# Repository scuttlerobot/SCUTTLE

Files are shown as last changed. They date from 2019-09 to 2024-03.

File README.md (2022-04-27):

# SCUTTLE™ Robot
This repository contains software (embedded Linux & Python) and hardware design files for the SCUTTLE Project.

### Sensing, Connected, Utility Transport Taxi for Level Environments
* payload capable (40kg)
* maker-friendly
* open source
* low-cost

### Visit the [SCUTTLE™ Webpage](https://scuttlerobot.org).
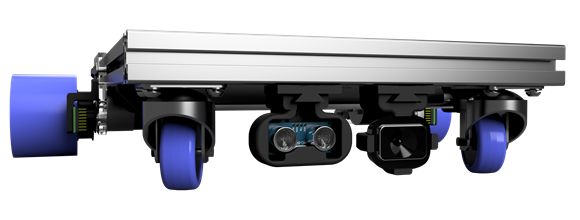
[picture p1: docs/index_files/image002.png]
SCUTTLE Robot


### License
This work is licensed under the Creative Commons Attribution-ShareAlike 4.0 License.  To view details [visit creativecommons.org](https://creativecommons.org/licenses/by-sa/4.0/legalcode)

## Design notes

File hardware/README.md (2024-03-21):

# SCUTTLE™ Hardware
This directory contains hardware for standard SCUTTLE components.
* STL files for 3D printing
* 2D Drawings

Note: heavy models and elaborate CAD is stored OUTSIDE github to keep the repository lightweight.

## Jump to V3.0 model
Full assembly is posted on grabCAD
[grabCAD SCUTTLE v3.0](https://grabcad.com/library/scuttle-robot-v3-0-1)
As upgrades are made to individual systems, we post individual models and describe them at scuttlerobot.org.

## Important models
Are archived on our website at
[scuttlerobot.org/resources/models](https://https://www.scuttlerobot.org/resources/models/)

## Native CAD files
Are primarily posted on grabCAD using keyword: "scuttle robot"
[search grabCAD](https://grabcad.com/library?page=2&time=all_time&sort=recent&query=scuttle%20robot)

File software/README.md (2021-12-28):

# SCUTTLE Software
This folder contains all scuttle software and software information.

<br>

## SHELL Processes Cheat Sheet:
**Remove your Tamulink WPA credentials from the device:**
* Navigate to the connmanctl folder located at /var/lib/connman$
* Find the configuration file with extension .config
* remove the config file with "rm."  Example: 
```
debian@scuttle:/var/lib/connman$ sudo rm wifi_8030dc035d88_74616d756c696e6b2d777061_managed_ieee8021x.config
  ```

**Report devices active on the i2c bus:**
```
sudo i2cdetect -y -r 1

  sudo:       Executes the command following as root user
  i2cdetect:  A program to scan an I2C bus for devices
  -y  :       Does not prompt
  -r 1:       I2C bus to read from. Here we read from I2C bus 1.
  ```

**Report the messages from kernel ring buffer (system architecture, cpu, attached devices, etc)**
```
dmesg
  ```
  
**Check battery voltage (with example output)**
```
➜  ~ sudo rc_battery_monitor
2S Pack   Jack   #Cells   Cell
 8.22V   10.63V  3       3.54V   [1]    1088 killed     sudo rc_battery_monitor

  ```
**List USB devices connected (with example output)**
  ```
➜  ~ lsusb
Bus 001 Device 003: ID 2f24:0091
Bus 001 Device 001: ID 1d6b:0002 Linux Foundation 2.0 root hub
  ```

**Explicitly Show Debian Release Date**
  ```
debian@scuttle:~$ cat /etc/dogtag
BeagleBoard.org Debian Image 2018-10-07

  ```
  
**Check if you have a live internet connection**
  ```
debian@scuttle:~$ ping google.com
PING google.com (216.58.194.110) 56(84) bytes of data.
64 bytes from dfw06s48-in-f14.1e100.net (216.58.194.110): icmp_seq=1 ttl=55 time                                       =10.5 ms
64 bytes from dfw06s48-in-f14.1e100.net (216.58.194.110): icmp_seq=2 ttl=55 time                                       =16.3 ms
64 bytes from dfw06s48-in-f14.1e100.net (216.58.194.110): icmp_seq=3 ttl=55 time                                       =17.8 ms
64 bytes from dfw06s48-in-f14.1e100.net (216.58.194.110): icmp_seq=4 ttl=55 time                                       =16.5 ms
^C
--- google.com ping statistics ---
4 packets transmitted, 4 received, 0% packet loss, time 3005ms
rtt min/avg/max/mdev = 10.521/15.320/17.869/2.835 ms
  ```

**Manually Connect to the internet**
<br>
Use commands: sudo connmanctl, scan wifi, agent on, services, connect (service)
<br>
[see steps and example output here](https://gist.github.com/dmalawey/e4be9f3b5beba8ed49868065935127b7)

**Copy a GitHub repository to your device**
  ```
debian@scuttle:~$ git clone http://github.com/scuttlerobot/SCUTTLE
Cloning into 'SCUTTLE'...
remote: Enumerating objects: 262, done.
remote: Counting objects: 100% (262/262), done.
remote: Compressing objects: 100% (215/215), done.
remote: Total 1356 (delta 128), reused 99 (delta 41), pack-reused 1094
Receiving objects: 100% (1356/1356), 82.88 MiB | 1.17 MiB/s, done.
Resolving deltas: 100% (610/610), done.
debian@scuttle:~$
  ```

**Expand the partition on your Blue SD card**
  ```
cd /opt/scripts/tools #navigate to the right directory
git pull  #update the tools repository
sudo ./grow_partition.sh  # the command to expand the boot partition
sudo reboot # the command to reboot the blue
  ```
  
**Print the current connections**
  ```
sudo iwconfig
  ```
  
**Copy a github repository**
  ```
git clone http://www.github.com/scuttlerobot/SCUTTLE
  ```
  This will copy all of the contents of SCUTTLE repo into a folder called SCUTTLE in the working directory.
  
**github - push updates from local to online repository**
  ```
git add -A
git commit -m # then make brief comment on your update
git push # then provide credentials as needed
  ```
  This will push the updates from your local device back to the online repo.

**github - pull updates from online to local repository**
  ```
git pull
  ```
  This will pull updates from online.  If it has conflicts and you want to force it, follow the steps in [this link](https://learn.adafruit.com/an-introduction-to-collaborating-with-version-control/https-credential-caching-and-ssh-keys).
  
## Windows Cheat Sheet:
**find out the IP address of a connected device**
Press the windows key, type "cmd" then ENTER.  In the command prompt, type ipconfig.  If you are connected to your linux device that is in access-point mode with your wireless wifi adapter, look at Wireless LAN section and the Default Gateway is the IP address of your linux device.

```
Wireless LAN adapter Wi-Fi:
   Connection-specific DNS Suffix  . :
   Link-local IPv6 Address . . . . . : fe80::8123:73e7:ace0:720c%15
   IPv4 Address. . . . . . . . . . . : 192.168.50.50
   Subnet Mask . . . . . . . . . . . : 255.255.255.0
   Default Gateway . . . . . . . . . : 192.168.50.1
```

## Beaglebone Blue Cheat Sheet:

**Default Wifi**
<br>Access Point SSID: BeagleBone-XXXX
<br>Password: BeagleBone

**Need extra help troubleshooting?**
<br/>
([beaglebone Live Chat](https://beagleboard.org/chat))
<br/>
Make sure 1) it's a beagle related issue 2) you give 30 minutes for an expert to respond (they will!) before you close the window. 3) If you learn something helpful for the project, share with our github admins

**Important ip addresses:**
<br/>
192.168.8.1:22 default terminal session over wifi <br/>
192.168.7.2:22 default terminal session over USB <br/>
192.168.8.1:3000 Cloud9 (over wifi) <br/>
192.168.8.1:1880 Nodered (over wifi) <br/>

**Instructions to connect to SSH using putty:**
<br/>
([beaglebone how-to-connect](https://www.dummies.com/computers/beaglebone/how-to-connect-your-beaglebone-via-ssh-over-usb/))

**Instructions to flash a new SD card with an image:**
<br/>
([beagleboard.org getting started](http://beagleboard.org/getting-started#step3))

**Access NodeRed:**
<br/>
Navigate to nodered: 192.168.8.1:1880

**Reinstall RCPY/librobotcontrol if it becomes corrupted**
<br/>
sudo apt-get purge roboticscape <br/>
sudo apt-get install librobotcontrol

**A Tool for Pin Checking:**
<br/>
This tool is great for debugging connections to pins. <br/>
([Pin configuration viewer tool, nicely formatted.](https://github.com/mvduin/bbb-pin-utils/tree/blue#show-pins))

## Raspberry Pi Cheat Sheet:
**Instructions to connect to SSH using putty:**
([beaglebone how-to-connect](https://www.dummies.com/computers/beaglebone/how-to-connect-your-beaglebone-via-ssh-over-usb/))

**Instructions to flash a new SD card with an image:**
([beagleboard.org getting started](http://beagleboard.org/getting-started#step3))

**broadcom BCM pin numbering scheme:**
https://gpiozero.readthedocs.io/en/stable/recipes.html#pin-numbering

# Linux Cheatsheet

### File System Navigation and Information

`ls` - **List** - List the files and folders in a directory.<br>
`cd` - **Change Directory** - Move into a folder.<br>
`pwd` - **Print Working Directory** - Prints your current location to the terminal.<br>
`cp` - **Copy** - Copies a file from a location, to a location.<br>
`mv` - **Move** - Moves a file from a location, to a location.<br>
`touch` - **Touch** - Create a file.<br>
`mkdir` - **Make Directory** - Make a directory with given name.<br>
`nano` - File editor.<br>
`cat` - **Concatenate** - Concatenate files and print file contents to the terminal.<br>
`head` - Output the first part of files.<br>
`tail` - Output the last part of files.<br>
`more` - View a file and scroll through it.<br>
`less` - View a file and scroll through it. (Consumes less resources than `more`)<br>
`rm` - **Remove** - Remove files or directories.<br>
`rmdir` - **Remove Directory** - Remove empty directories.<br>
`file` - Determine file type.<br>

### System and User Info

`whoami` - **Who Am I?** - Print current user.<br>
`date` - Print or set the system date and time.<br>
`df` - Report file system disk space usage.<br>
`which` - Locate a command.<br>
`whereis` - Locate the binary, source, and manual page files for a command.<br>

### Searching

`grep` - Print lines that match patterns.<br>
`locate` - Find files by name.<br>

### Administrator

`sudo` - **Superuser Do** - Execute a command as root(superuser).<br>
`sudo su` - Switch to the root user.<br>

### Modify Permissions

`chown` - **Change Owner** - Change ownership of a file.<br>
`chmod` - **Change Mode** - Change file mode bits.<br>

### Network Information

`ping` - Send ICMP ECHO_REQUEST to network hosts.<br>
`ifconfig` - Configure a network interface.<br>
`iwconfig` - Configure a wireless network interface.<br>
`connmanctl` - **Connection Manager** - WiFi connection Utility.<br>

### Web Tools

`wget` - **Web Get** - Get a file from a server.<br>

### Process Management and Resource Monitoring

`top` - Display Linux processes & CPU (processor) load.<br>
`htop` - Interactive process viewer.<br>
`kill` - Kill a process.<br>
`time` - Run programs and summarize system resource usage.<br>

### Installing Programs and Libraries

`apt-get` - APT package handling utility.<br>
`pip` - A tool for installing and managing Python packages.<br>
`pip2` - A tool for installing and managing Python2 packages.<br>
`pip3` - A tool for installing and managing Python3 packages.<br>

### Running Code and Scripts

`sh` - **SHell** - Command interpreter.<br>
`bash` - **Bourne Again SHell** - Command interpreter. (More updated than `sh`)<br>
`python` - Python interpreter (typically defaults to python2).<br>
`python2` - Python2 interpreter.<br>
`python3` - Python3 interpreter.<br>

### USB Information

`lsusb` - **List USB** - list USB devices.<br>

### Script Commands

`echo` - Display a line of text.<br>
`sleep` - Sleep for a specified number of seconds.<br>

### Command Help

`man` - **Manual** - an interface to the on-line reference manuals.<br>
`whatis` - **What Is** - display one-line manual page descriptions.<br>

### Power

`reboot` - Restart the device.<br>
`shutdown` - Power-off the device.<br>

### Other Helpful Commands

`ssh` - **Secure SHell** - OpenSSH SSH client. (remote login program)<br>
`git` - Code version control suite.<br>

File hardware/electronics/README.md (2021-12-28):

## SCUTTLE Electronics

This folder contains electronics design files for SCUTTLE.
<br>Wiring diagrams are found on the [SCUTTLE Webpage](https://scuttlerobot.github.io/SCUTTLE)

### PCB Design Files
Gerber files are zipped and shared here for our i2c breakout board.

**How to Order a Custom PCB:** <br>
* Go to the quotes page at JLCPCB.com [Here](https://jlcpcb.com/quote#/) <br>
* Upload the zip file containing the designs <br>
* Proceed to order. <br>
* Cost: As of 2020, you can get 30 boards for $22.51 (shipping included!)

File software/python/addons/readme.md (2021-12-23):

Here you'll find Python software for adding features to your robot

SICK TIM561 EXAMPLE
1) Mount your TIM561 to your robot, plug the power into your 12v battery pack, and connect the microUSB cable from your embedded device to your LIDAR. <br>
2) Install pyusb using `sudo pip3 install pyusb`
3) install pysicktim library on your device using `sudo pip3 install pysicktim`. <br>
4) run the example using python3

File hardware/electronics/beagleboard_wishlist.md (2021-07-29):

## Wishlist for Beaglebone Blue upgrades by the SCUTTLE team:
#### STATUS: (re-collecting input from previous document as of 07.20)

### Performance Requests
* Charging & power sourcing from 3 cell LiPo batteries
* Servos must be able to be run from BOTH liPo and barrell jack, independently
* Keep at least 2 motor outputs based on PRU for high frequency driving
* make at least 4 hardware PWM outputs at TTL voltage [#313](https://github.com/adafruit/adafruit-beaglebone-io-python/issues/313#issuecomment-513881299)
* desired: increase digital GPIO input count (currently 2?) [#313](https://github.com/adafruit/adafruit-beaglebone-io-python/issues/313)
* Maintain UART function when utilizing software PWM output [#313](https://github.com/adafruit/adafruit-beaglebone-io-python/issues/313)

### Interfacing Requests - High Impact
* keeping 2 wifi hardware module is great
* gold plated pins for motors and servos to support higher current
* for I2C bus: convert JST-SH connectors to QWIIC connector shape & pin config
* countermeasure the motor output pins plastic cowling - they slide off

### Hardware Requests - Medium Impact
* Motor outputs that supports 12v 2A each
* Include reverse polarity protection on barrel power input

### Other Comments
* 5gHz wifi is low priority (to date)
* Motors functions: The need for SCUTTLE is EITHER A) drive motors at TTL voltages, with no need for high current OR B)make motor drivers able to output 12v and sufficient current.

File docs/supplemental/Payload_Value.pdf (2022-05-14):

73

10 | 11
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
SCUTTLE Freight
100

Waffle Pi MiR 100 Panther Rover Zero 2

Otto 100 Jackal

KG PER $1000

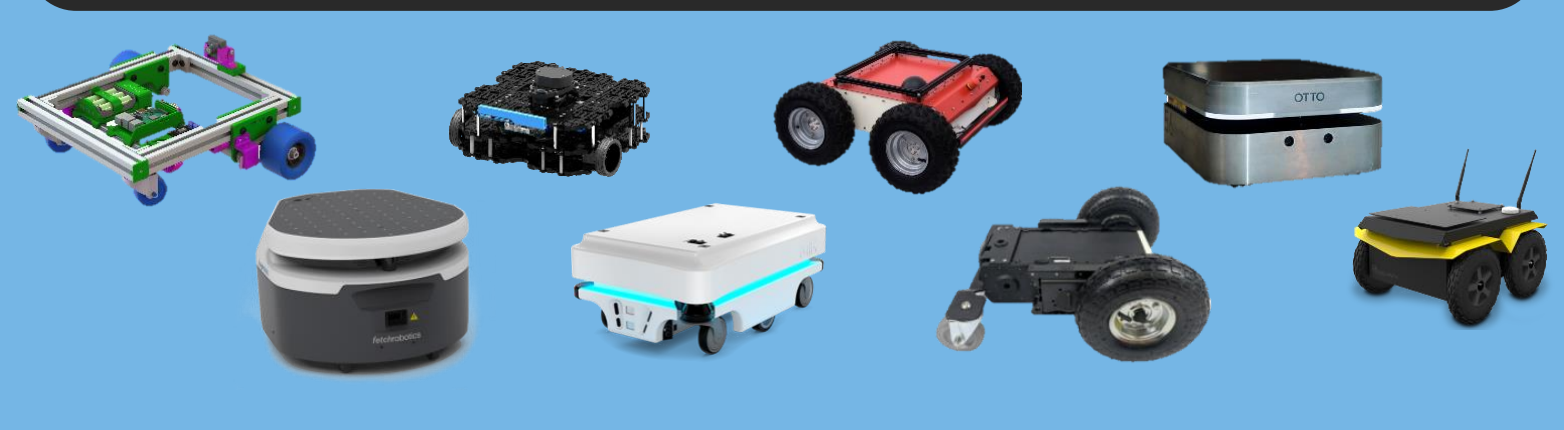
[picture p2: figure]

Product Name Price (USD) Payload (kg) Kg Per $1000 | Website
SCUTTLE | $520 | 40 | 77 | SCUTTLE (https://scuttlerobot.org/)
Freight 100 * | $10,000 | 100 | 10 | Fetch Robotics (https://fetchrobotics.com/freight100-base/)
Waffle Pi | $1,499 | 30 | 20 | Turtlebot (https://www.robotlab.com/store/robotis-turtlebot-openmanipulator)
MiR 100 | $24,000 | 100 | 4 | MIR (https://www.designworldonline.com/robots-save-employees-1000-miles-walking-annually/)
Panther | $12,580 | 80 | 6 | Husarion (https://husarion.com/manuals/panther/)
Rover Zero 3 | $3,499 | 75 | 21 | RoverRobotics (https://roverrobotics.com/collections/all/products/copy-of-4wd-rover-zero-3)
Otto 100 * | $24,000 | 100 | 4 | Otto Motors (https://ottomotors.com/100)
Jackal | $12,000 | 17 | 1 | Clearpath (https://clearpathrobotics.com/)
Vector * | $15,000 | 136 | 9 | Waypoint Robotics (https://waypointrobotics.com/vector-robotic-mobility-platform/)
ROSbot 2.0 | $2,199 | 2 | 1 | Husarion (https://store.husarion.com/products/rosbot)
Boxer | $42,000 | 60 | 1 | Clearpath Robotics (https://clearpathrobotics.com/boxer/)
Omron LD-60 | $2,399 | 60 | 25 | Omron Lineup (https://www.ia.omron.com/products/family/3664/lineup.html)
Leorover | $250 | 5 | 20 | LeoRover.tech (https://www.leorover.tech/the-rover)
*pricing is estimated because it is not disclosed for these units

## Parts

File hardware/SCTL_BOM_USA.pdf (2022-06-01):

6/1/2022

category | Store | Part | PN

cost
(each)

qty
needed | subtotal | Last updated
chassis | amazon | Wheel, urethane 83mm, with bearings (pair) | B07531B4GK | $16.23 | 1 | $16.23 | 2022.05
chassis | amazon | Bracket - 90deg aluminum, (for chassis) with M6 Screw (2) and 3030 T-nut(2) | B07BQR7WX8 | $2.75 | 4 | $10.99 | 2021.10
chassis | Mcmaster | Timing Belt, 5mm pitch, 245mm length, 9mm width | B08PW2HD81 | $6.43 | 2 | $12.86 | 2022.05
chassis | Mcmaster | Hex Nut, M8 (for axle) | 90591A161 | $0.07 | 2 | $0.14 | 2021.10
chassis | Mcmaster | T-slot Framing Extrusion - 30mm x 1ft (for chassis) | 5537T97 | $8.13 | 4 | $32.52 | 2022.05
chassis | amazon | Caster wheels (for front) | B01J4FED5E | $1.83 | 2 | $3.67 | 2022.05
chassis | Mcmaster | Screws - M8x110mm screw (axles) | 91290A470 | $0.97 | 2 | $1.95 | 2022.05
chassis | Mcmaster | Screws, M6 x 14mm (for motor plates) | 91239A319 | $0.10 | 8 | $0.82 | 2019.11
chassis | Mcmaster | Screws - M6 x 10mm (for casters & chassis brackets) | 91239A316 | $0.10 | 12 | $1.25 | 2019.11
chassis | McMaster | Screw, set screw, M5x0.6 (for motor pulley) | 91390A118 | 0.04 | 2 | $0.08 | 2019.11
chassis | Mcmaster | Screw, Flat head, M3x10mm (for motors 6) | 92010A120 | $0.04 | 6 | $0.27 | 2019.11
chassis | amazon | Screw, self-tapping, M2 x 6mm, for plastic (for encdr brkt 4, ultrsnc brkt 4) | B00GMQDSRI | 0.01 | 8 | $0.07 | 2019.11
chassis | Mcmaster | Screw, M2.5x10mm countersunk (for battery case) | 92010A020 | 0.04 | 6 | $0.23 | 2019.11
chassis | Mcmaster | Screw, M2.5x6mm pan head (for motor driver mount 2, bbb lid 1) | 92005A066 | 0.04 | 3 | $0.13 | 2019.11
chassis | amazon | Nut, M6 nickel-plated steel for 3030 T-slot extrusion | B077Z2HX42 | $0.20 | 12 | $2.40 | 2019.11
chassis | Mcmaster | Washer, lock washer for M8 bolt (for axles) | 92148A200 | 0.07 | 2 | $0.15 | 2019.11
chassis | Mcmaster | Washer, flat washer for M8 Bolt (for axles) | 93475A270 | 0.08 | 2 | $0.16 | 2019.11
chassis | Mcmaster | Washer, 6x12mm (wheelBrackets) | 93475A250 | 0.05 | 8 | $0.43 | 2019.11
chassis | Mcmaster | Washer, M6, split lock (for casters) | 91202A234 | 0.03 | 6 | $0.17 | 2019.11
chassis | Mcmaster | Tubing, 1/2 in OD, 6063, aluminum, sold 8ft section, price per ft | 1658T13 | 2.12 | 1.6 | $3.38 | 2019.11
chassis | Mcmaster | Threaded insert, M2.5 x 3.4 heat set (btry 2, whlplts 4, m.driver 2) | 94180A321 | 0.12 | 9 | $1.11 | 2019.11
Subtotal | $89.00
SBC | mouser | Raspberry Pi 4, 2gb RAM | 713-102991317 | 56.25 | 1 | $56.25 | 2022.05
actuator | amazon | Motor Driver Board with Twin MC33886 H-Bridges (HW-231 model) | B07VHFCYFQ | 16.41 | 1 | $16.41 | 2022.05
actuator | amazon | Motor, DC 12v with 200 rpm gearbox (for drivetrain) | B072R5QSRG | 14.99 | 2 | $29.98 | 2022.05
Sensors | amazon | Camera, USB, 2.1mm focal len, 150 deg FOV, | B07QSTPGR8 | 58.99 | 1 | $58.99 | 2022.05
power | amazon | Battery cell, Panasonic 18650 or other brand | B00GS48XRE | 7.48 | 3 | $22.45 | 2019.11
Sensors | mouser | Encoder, AMS5048B, circuit boards | 990600491 | 15.75 | 2 | $31.50 | 2022.05
connectors | powerwerx | Anderson PowerPole Connectors, 30amp | WP30-100 | 1.15 | 8 | $9.24 | 2019.11
power | digikey | Battery Tray, 3 cell li-ion (BK-18650-PC6 on digikey) | BK-18650-PC6 | 2.00 | 1 | $2.00 | 2019.11
power | mouser | Switch, rocker, SPST 10A BLK ON-OFF Symbols (for battery case) | SRB22A2FBBNN | 0.95 | 1 | $0.95 | 2019.11
power | amazon | Terminals - 22-16 AWG Insulated Female Quick Connect Terminal | B06XCWFTJ9 | 0.13 | 2 | $0.26 | 2019.11
power | amazon | Power Wire - 18 AWG (black/red pair), price listed per meter | B07428NBCW | 0.69 | 1 | $0.69 | 2019.11
Wiring | amazon | Cable, 20cm ribbon, with female Dupont terminals (i2c board ►encoders) | B07GCY6CH7 | 1.06 | 1 | $1.06 | 2022.06
Wiring Pi | amazon | Cable, 10cm ribbon, with female Dupont terminals (pi►motor driver) | B07GD312VG | 0.29 | 1 | $0.29 | 2022.06
Wiring BBB | amazon | Connector - JST SH 1.0mm 4-Pin with 100mm cable (for ultrasonic, encoders) | B01DUC1M2O | 0.40 | 2 | $0.80 | 2019.11
Wiring BBB | amazon | Connector - JST ZH 1.5mm 2 pin (for motor driver) | B074CFF5MT | 0.27 | 2 | $0.53 | 2019.11
Wiring BBB | amazon | Connector - JST SH 1.0mm 6-pin with 100mm cable (for ultrasonic sensor) | B0762K143K | 0.73 | 1 | $0.73 | 2019.11
Wiring BBB | amazon | Connector - barrell, 5.5x2.1mm, power (for beaglebone) | B076JCNFMP | 0.50 | 1 | $0.50 | 2019.11
power | amazon | battery management system (BMS) circuit board, 3S, 40A | B07JMY631D | 10.69 | 1 | $10.69 | 2019.11
power | amazon | battery cell charger, 18650 | B08DNQXB1C | 13.99 | 1 | $13.99 | 2022.05
Subtotal | $232.63
3D Print | Amazon | Filament, blue ABS Novamaker 1.75mm (1kg) | B07D6BG8FR | 19.99 | 0.42 | $8.48 | 2022.05
Wiring | JLCPCB | Custom PCB (this is optional) | upload design | 1.99 | 1.00 | $1.99 | 2019.11
Subtotal | $8.48
| $330.10
off-the-shelf | amazon | EasySMX model 9101 2.4GHz Game Pad Controller, with USB dongle | B01KV7B2CG | 29.99 | 1 | 29.99 | 2022.05
amazon | electronics | audio driver adapter (for beaglebone setup) | B07L56C28R | 10.50 | 1 | 10.50 | 2021.10
amazon | electronics | Speaker, using USB for power and signal | B087D2BPBC | 15.98 | 1 | 15.98 | 2021.10
amazon | electronics | 2s liPo battery (to enhance servos on beagle), 400mAh | B072BH1XP6 | 8.50 | | | 2019.11
amazon | hardware | m6 tslot nuts (drop-in nuts) | B08BHZ219C | 7.99 | 1 | 7.99 | 2022.05
Sensors | amazon | Ultrasonic distance sensor | B06XBV54WF | 1.599 | 1 | 1.60 | 2019.11
Sensors | amazon | lidar, Slamtec RPLidar, A1M8 (tested low-cost lidar) | B0923RYT8V | 99.99 | 1 | 99.99 | 2022.05
Copyright 2022 SCUTTLE Robotics LLC | Extras Total | $166.05

Extras

SCUTTLE BOM-USA LAST UPDATED:

Grand Total

Mechanical

Electronics

Custom

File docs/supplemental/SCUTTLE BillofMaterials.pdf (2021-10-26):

10/26/2021
category | Store | Part | PN | cost
| | | | (each) | qty
| | | | | needed | subtotal | Last updated
chassis | amazon | Wheel, urethane 83mm, with bearings & spacers (pair) | B084SNCXLG | $16.23 | 1 | $16.23 | 10/26/2021
chassis | amazon | Bracket - 90deg aluminum, (for chassis) with M6 Screw (2) and 3030 T-nut(2) | B07BQR7WX8 | $2.75 | 4 | $10.99 | 10/26/2021
chassis | Mcmaster | Timing Belt, Dust-Free, T5 Series, Trade No. T5-245-10 | 1679K451 | $4.94 | 2 | $9.88 | 10/26/2021
chassis | Mcmaster | Hex Nut, M8 (for axle) | 90591A161 | $0.07 | 2 | $0.14 | 10/26/2021
chassis | Mcmaster | T-slot Framing - 30mm x 1ft (for chassis) | 5537T97 | $6.29 | 4 | $25.16 | 10/26/2021
chassis | amazon | Caster wheels (for front) | B01J4FED5E | $1.92 | 2 | $3.83 | 2019.11
chassis | Mcmaster | Screws - M8x110mm screw (axles) | 91290A470 | $1.16 | 2 | $2.32 | 2019.11
chassis | Mcmaster | Screws, M6 x 14mm (for motor plates) | 91239A319 | $0.10 | 8 | $0.82 | 2019.11
chassis | Mcmaster | Screws - M6 x 10mm (for casters & chassis brackets) | 91239A316 | $0.10 | 12 | $1.25 | 2019.11
chassis | McMaster | Screw, set screw, M5x0.6 (for motor pulley) | 91390A118 | 0.04 | 2 | $0.08 | 2019.11
chassis | Mcmaster | Screw, Flat head, M3x10mm (for motors 6) | 92010A120 | $0.04 | 6 | $0.27 | 2019.11
chassis | amazon | Screw, self-tapping, M2 x 6mm, for plastic (for encdr brkt 4, ultrsnc brkt 4) | B00GMQDSRI | 0.01 | 8 | $0.07 | 2019.11
chassis | Mcmaster | Screw, M2.5x10mm countersunk (for battery case) | 92010A020 | 0.04 | 6 | $0.23 | 2019.11
chassis | Mcmaster | Screw, M2.5x6mm pan head (for motor driver mount 2, bbb lid 1) | 92005A066 | 0.04 | 3 | $0.13 | 2019.11
chassis | amazon | Nut, M6 nickel-plated steel for 3030 T-slot extrusion | B077Z2HX42 | $0.20 | 12 | $2.40 | 2019.11
chassis | Mcmaster | Washer, lock washer for M8 bolt (for axles) | 92148A200 | 0.07 | 2 | $0.15 | 2019.11
chassis | Mcmaster | Washer, flat washer for M8 Bolt (for axles) | 93475A270 | 0.08 | 2 | $0.16 | 2019.11
chassis | Mcmaster | Washer, 6x12mm (wheelBrackets) | 93475A250 | 0.05 | 8 | $0.43 | 2019.11
chassis | Mcmaster | Washer, M6, split lock (for casters) | 91202A234 | 0.03 | 6 | $0.17 | 2019.11
chassis | Mcmaster | Tubing, 1/2 in OD, 6063, aluminum, sold 8ft section, price per ft | 1658T13 | 2.12 | 1.6 | $3.38 | 2019.11
chassis | Mcmaster | Threaded insert, M2.5 x 3.4 heat set (btry 2, whlplts 4, m.driver 2) | 94180A321 | 0.12 | 9 | $1.11 | 2019.11
| | | | | Subtotal | $79.20
SBC | mouser | BeagleBone Blue | 95Y0640 | 82.00 | 1 | $82.00 | 2019.11
actuator | amazon | Motor Driver Board with Twin MC33886 H-Bridges (HW-231 model) | B07KGBJGCW | 13.99 | 1 | $13.99 | 2019.11
actuator | amazon | Motor, DC 12v with 200 rpm gearbox (for drivetrain) | B072R5QSRG | 14.99 | 2 | $29.98 | 2019.11
Sensors | amazon | Camera, Microsoft HD 3000 | B008ZVRAQS | 23.99 | 1 | $23.99 | 2019.11
power | amazon | Battery cell, Panasonic 18650 or other brand | B00GS48XRE | 7.48 | 3 | $22.45 | 2019.11
Sensors | mouser | Encoder circuit boards - AMS | 990600491 | 15.75 | 2 | $31.50 | 2019.11
connectors | powerwerx | Anderson PowerPole Connectors, 30amp | WP30-100 | 1.15 | 8 | $9.24 | 2019.11
power | digikey | Battery Tray, 3 cell li-ion (BK-18650-PC6 on digikey) | BK-18650-PC6 | 2.00 | 1 | $2.00 | 2019.11
power | mouser | Switch, rocker, SPST 10A BLK ON-OFF Symbols (for battery case) | SRB22A2FBBNN | 0.95 | 1 | $0.95 | 2019.11
power | amazon | Terminals - 22-16 AWG Insulated Female Quick Connect Terminal | B06XCWFTJ9 | 0.13 | 2 | $0.26 | 2019.11
power | amazon | Power Wire - 18 AWG (black/red pair), price listed per meter | B07428NBCW | 0.69 | 1 | $0.69 | 2019.11
Wiring BBB | amazon | Connector - JST SH 1.0mm 4-Pin with 100mm cable (for ultrasonic, encoders) | B01DUC1M2O | 0.40 | 2 | $0.80 | 2019.11
Wiring BBB | amazon | Connector - JST ZH 1.5mm 2 pin (for motor driver) | B074CFF5MT | 0.27 | 2 | $0.53 | 2019.11
Wiring BBB | amazon | Connector - JST SH 1.0mm 6-pin with 100mm cable (for ultrasonic sensor) | B0762K143K | 0.73 | 1 | $0.73 | 2019.11
Wiring BBB | amazon | Connector - barrell, 5.5x2.1mm, power (for beaglebone) | B076JCNFMP | 0.50 | 1 | $0.50 | 2019.11
power | amazon | battery management system (BMS) circuit board, 3S, 40A | B07JMY631D | 9.99 | 1 | $9.99 | 2019.11
| | | | | Subtotal | $219.61
3D Print | Amazon | ABS 3D Printing Filament (price per kg listed) | B07D6BG8FR | 18.99 | 0.42 | $8.05 | 2019.11
Wiring | JLCPCB | Custom PCB (this is optional) | upload design (https://github.com/MXET/SCUTTLE/blob/master/hardware/electronics/pcb_designs/I2C_Breakout_gerbers.zip) | 1.99 | 1.00 | $1.99 | 2019.11
| | | | | Subtotal | $8.05
| | | | | | $306.86
off-the-shelf | amazon | EasySMX 2.4GHz Game Pad Controller, with USB dongle | B01KV7B2CG | 32.99 | 1 | 33 | 10/26/2021
amazon | electronics | audio driver adapter (for beaglebone setup) | B07L56C28R | 10.50 | 1 | 11 | 10/26/2021
amazon | electronics | Speaker, using USB for power and signal | B087D2BPBC | 15.98 | 1 | 16 | 10/26/2021
automationdirect.comelectronics | lidar power cable (for SICK lidar) | 7000-12241-2150300 | 1 | 0 | 2019.11
amazon | hardware | 20 tooth timing belt pulley - for crane build | B019GICCMA | | | 0 | 2019.11
amazon | electronics | 2s liPo battery (to offer servos on beagle), 400mAh | B072BH1XP6 | 8.50 | | 0 | 2019.11
amazon | hardware | m6 tslot nuts (rotating) | b077z2hx42 | | | 0 | 2019.11
SICK USA | sensors | tiM561 LIDAR unit | | | | 0 | 2019.11
chassis | Mcmaster | Pulley - T5,28mm OD, for motor (upgrade from plastic - for drivetrain) | 1428N23 | $9.46 | 2 | $18.92 | 2019.11
Sensors | digilent | Compass Sensor - PMOD CMPS2 (beagleboard has a compass built-in) | 410-355 | 7.99 | 1 | $7.99 | 2019.11
Sensors | amazon | Ultrasonic distance sensor | B06XBV54WF | 1.599 | 1 | $1.60 | 2019.11

SCUTTLE BOM-USA LAST UPDATED:

Non-Essential

Grand Total

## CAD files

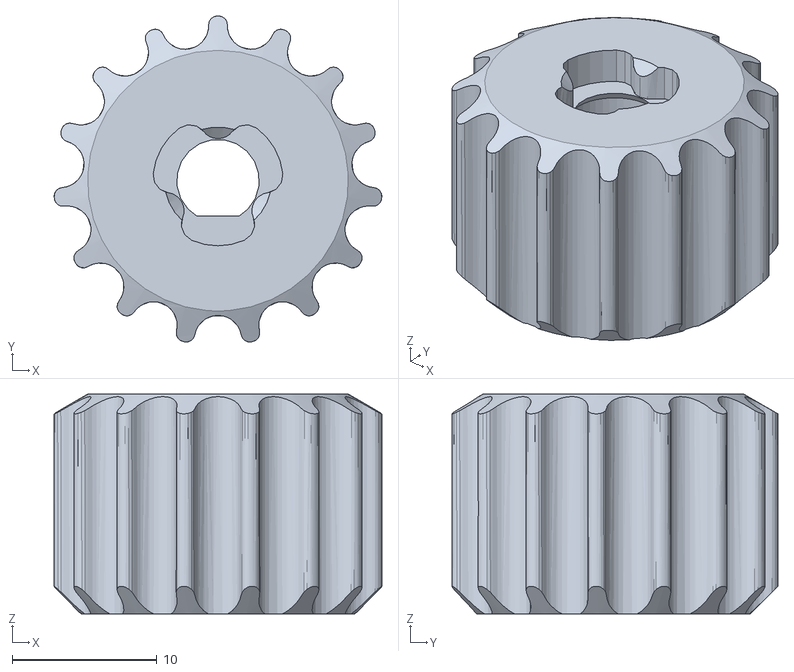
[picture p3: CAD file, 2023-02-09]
hardware/3D_Prints/mtrPuly_v3.4.STL
22.6 x 22.5 x 15.2

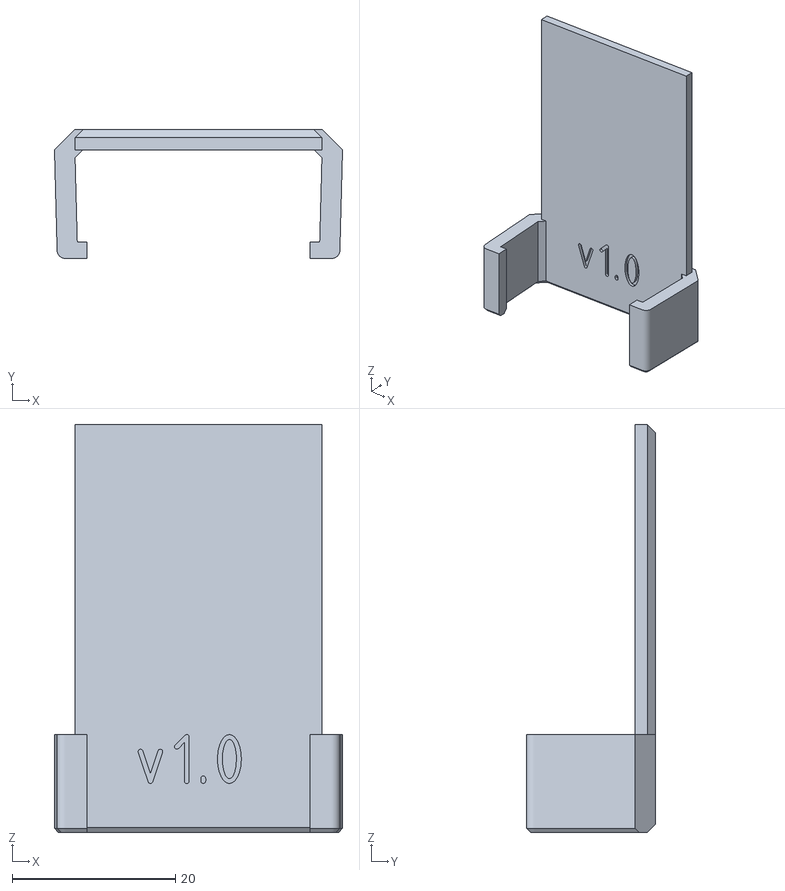
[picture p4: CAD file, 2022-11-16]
hardware/3D_Prints/serialTg_v1.0.STL
35.3 x 15.8 x 50.0

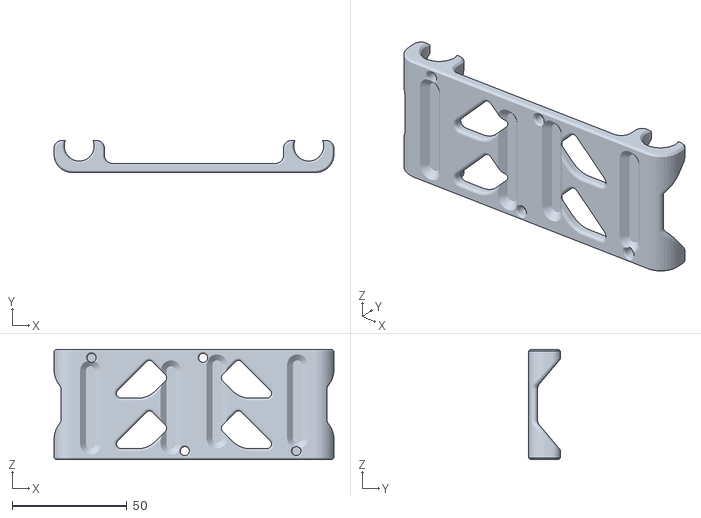
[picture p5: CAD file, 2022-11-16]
hardware/3D_Prints/mDrvBrkt_v1.5.STL
122.0 x 14.0 x 48.0

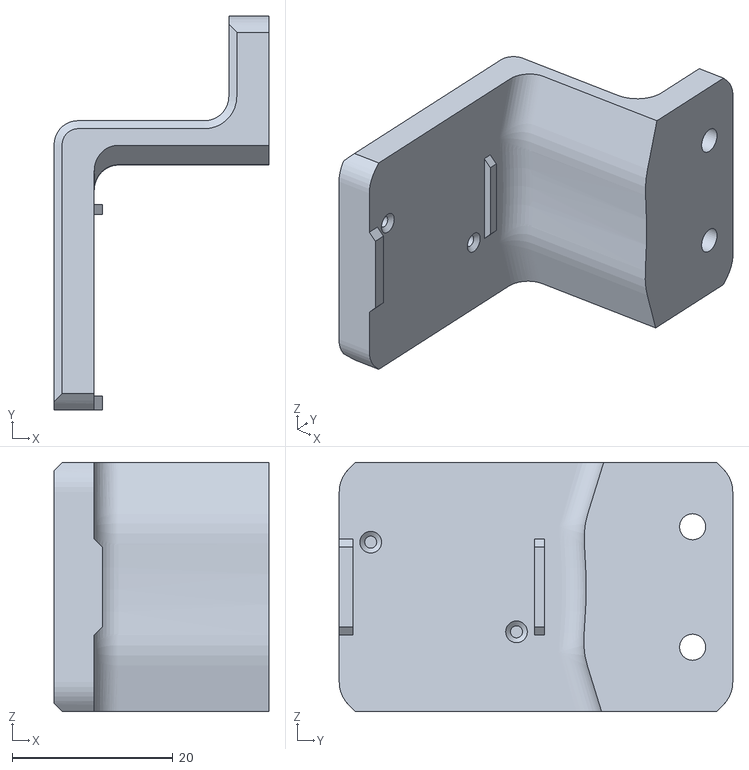
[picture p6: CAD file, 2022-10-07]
hardware/3D_Prints/encdrBrkt_v2.8.STL
26.7 x 49.0 x 31.0

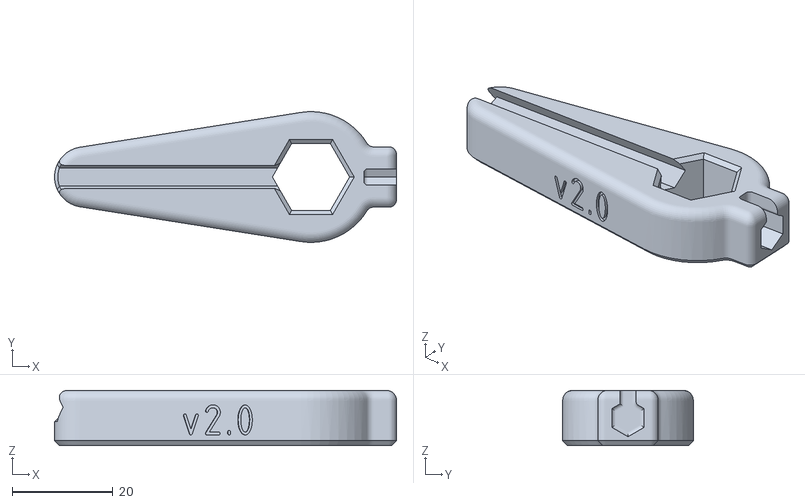
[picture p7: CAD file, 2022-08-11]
hardware/3D_Prints/wrench_v2.0.STL
68.0 x 26.0 x 11.0

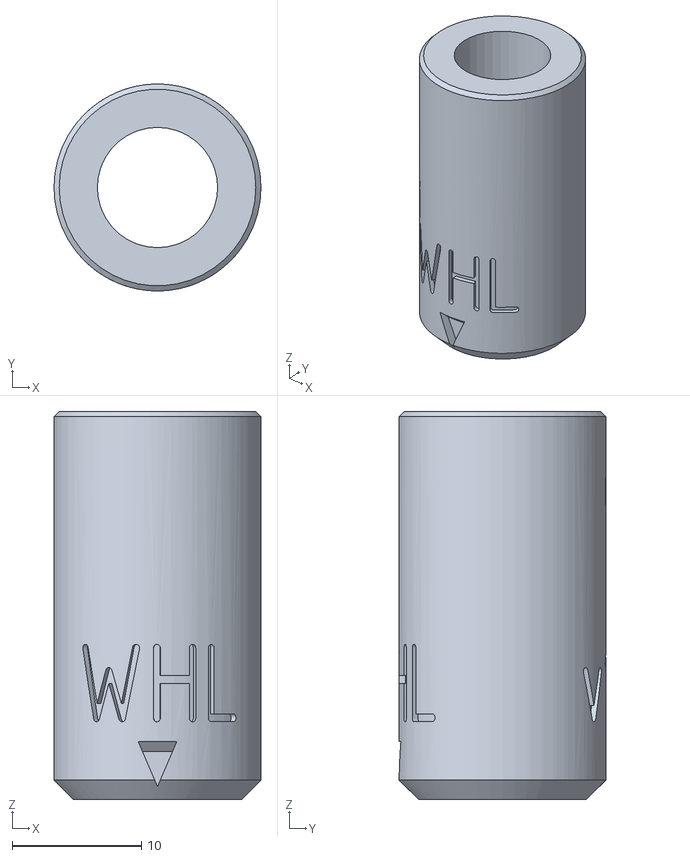
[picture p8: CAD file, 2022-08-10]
hardware/3D_Prints/wheelSpcr_v1.1.STL
16.0 x 16.0 x 30.0

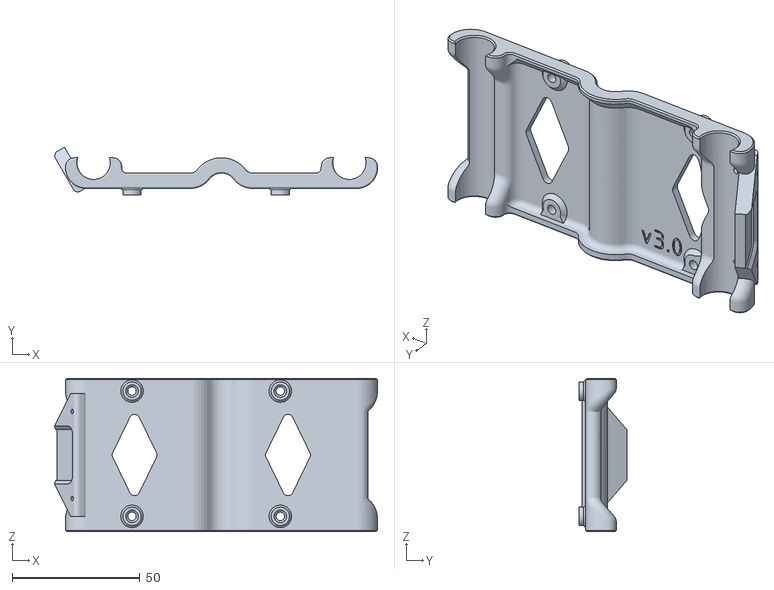
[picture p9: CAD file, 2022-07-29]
hardware/3D_Prints/cpuBrkt_v3.0.STL
126.3 x 18.6 x 60.0

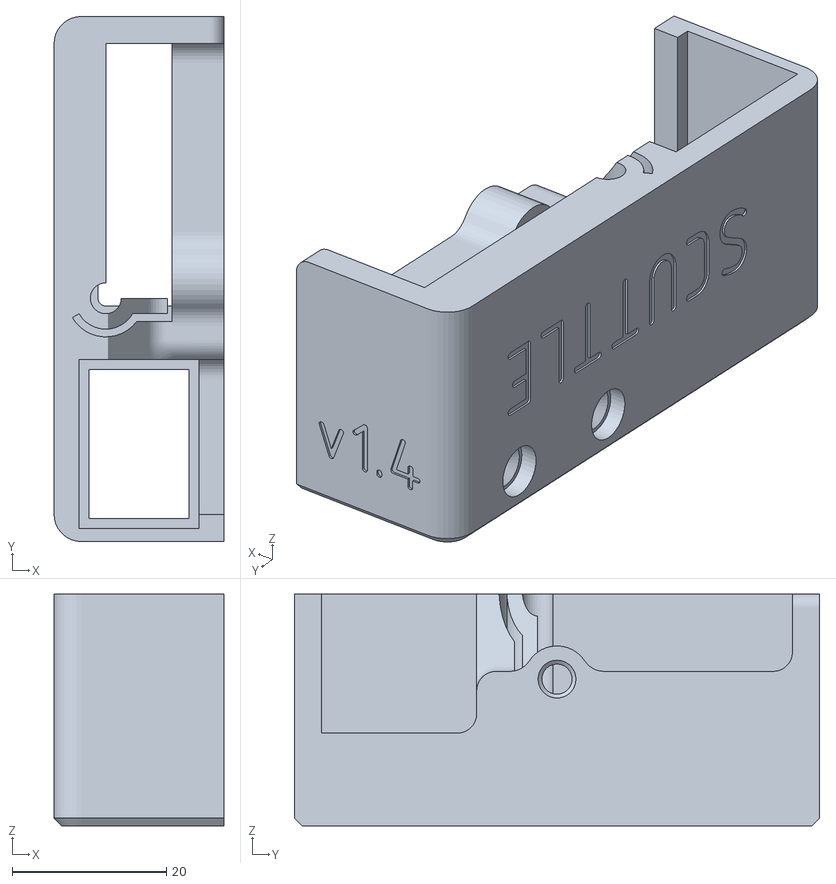
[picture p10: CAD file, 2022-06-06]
hardware/3D_Prints/btryPanel_v1.4.STL
22.0 x 68.0 x 30.0

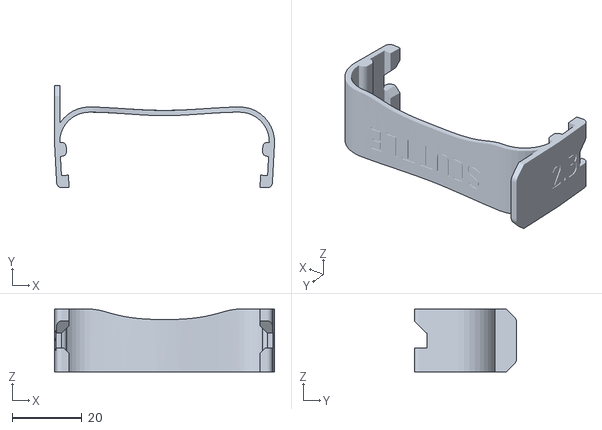
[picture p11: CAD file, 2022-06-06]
hardware/3D_Prints/btryHoop_v2.3.STL
63.0 x 29.3 x 18.0

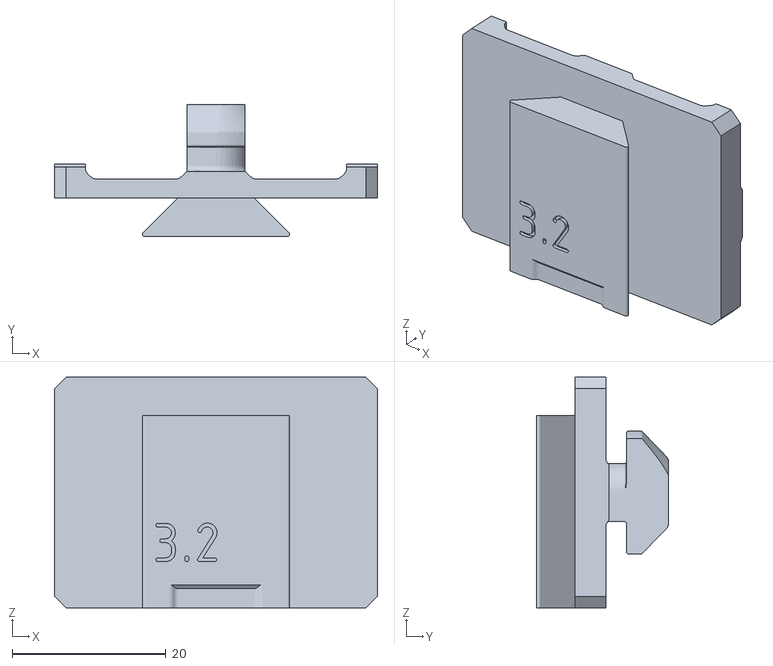
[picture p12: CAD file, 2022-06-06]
hardware/3D_Prints/twistBrkt_v3.2.STL
42.0 x 17.2 x 30.0

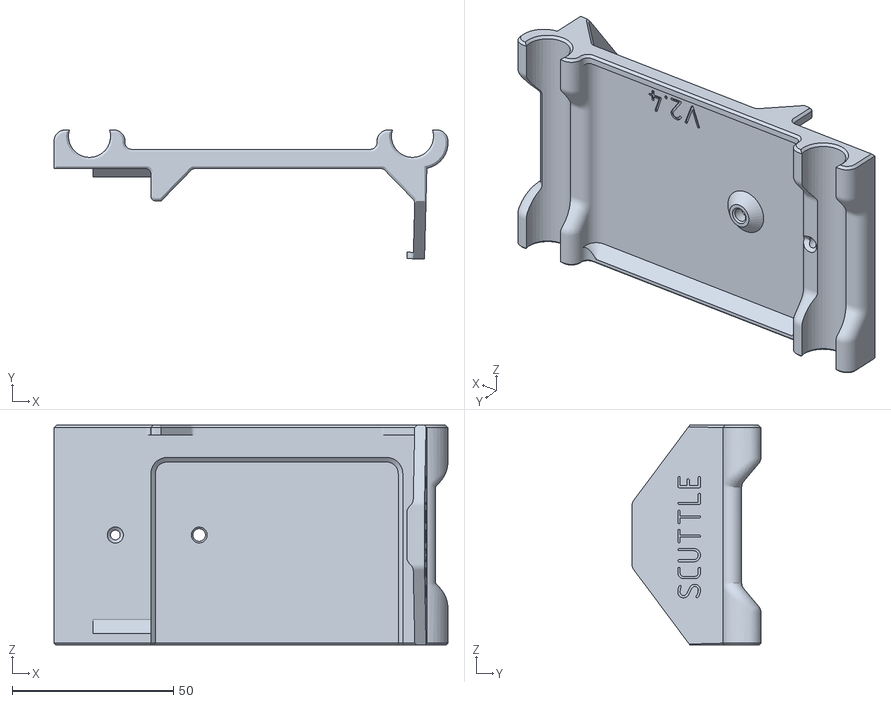
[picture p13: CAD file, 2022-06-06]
hardware/3D_Prints/btryBrkt_v2.4.STL
122.0 x 40.0 x 68.0

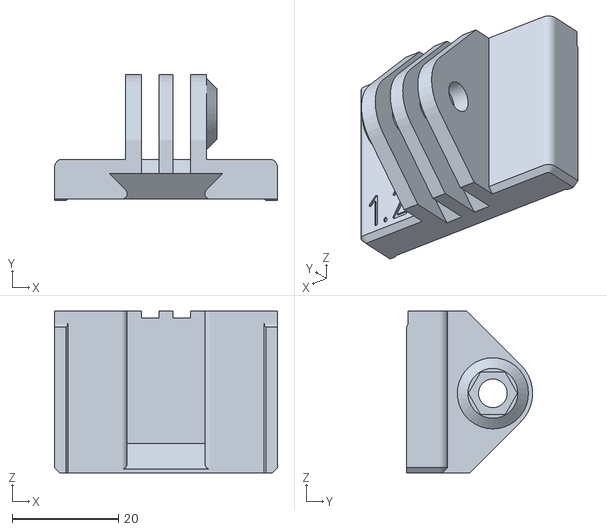
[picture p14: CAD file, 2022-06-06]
hardware/3D_Prints/cmraJnt_v1.2.STL
42.0 x 23.8 x 30.5

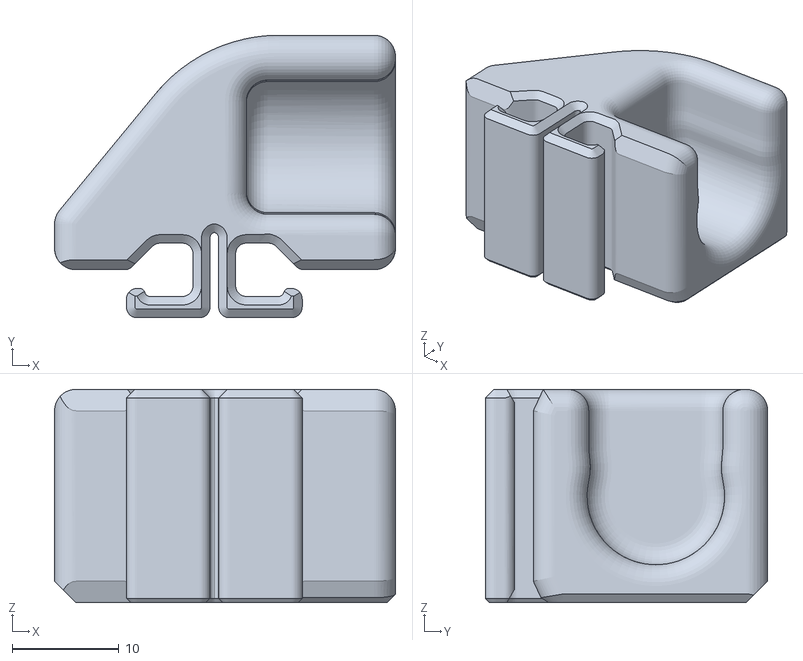
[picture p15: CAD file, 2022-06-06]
hardware/3D_Prints/rodBrkt_v4.2.STL
32.0 x 26.5 x 20.0

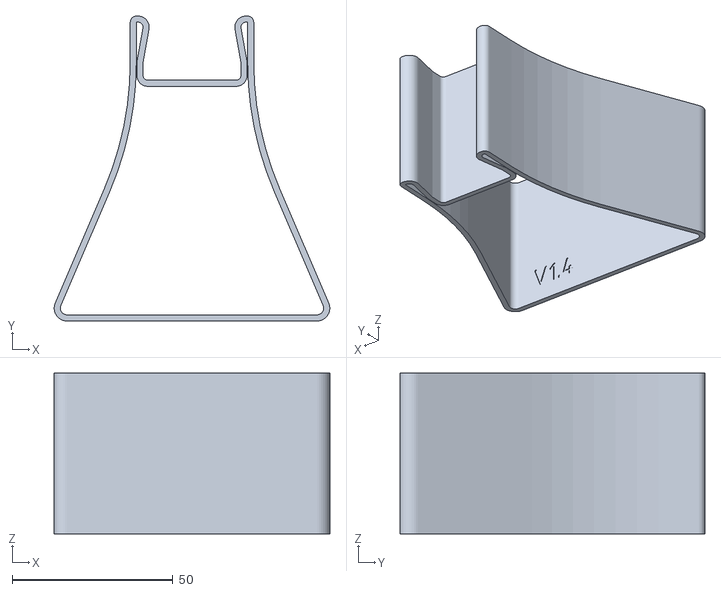
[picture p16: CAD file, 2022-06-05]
hardware/3D_Prints/kickStnd_v1.4.STL
85.8 x 95.0 x 50.0

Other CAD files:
hardware/3D_Prints/cmraBrkt_v3.0.STL
hardware/3D_Prints/wheelBrktL_v1.5.STL
hardware/3D_Prints/wheelBrktR_v1.5.STL
hardware/3D_Prints/wheelPuly_v3.3.STL

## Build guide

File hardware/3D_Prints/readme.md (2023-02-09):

## SCUTTLE™ 3D PRINTS
Updated: 2023.02, Using SCUTTLE v2.4

**Solidworks & STEP files on [GrabCAD](https://grabcad.com/library/scuttle-robot-v2-4-1)**
<br />
**Download [Excel Sheet](https://qr.scuttlerobot.org/g/1t9vwUOqvXf)**
<br />
**Discover our [Models Library](https://www.scuttlerobot.org/category/models)**

### Parts & Quantities: SCUTTLE v2.4
| Part Name | Part Version | Abbrev | Print Qty |
|---|---|---|-----|
| Rod bracket | 4.2 | rodBrkt_v4.2 | 4 |
| Encoder bracket | 2.8 | encdrBrkt_v2.8  | 2 |
| Motor Pulley | 3.4 | mtrPuly_v3.4 | 2 |
| Wheel Pulley | 3.3 | wheelPuly_v3.3  | 2 |
| Wheel Spacer | 1.1 | wheelSpcr_v1.1  | 2 |
| Battery Bracket | 2.4 | btryBrkt_v2.4 | 1 |
| Battery hoop | 2.3 | btryHoop_v2.3 | 1 |
| Battery panel | 1.4 | btryPanel_v1.4  | 1 |
| Camera bracket | 3.0 | cmraBrkt_v3.0 | 1 |
| Camera joint | 1.2 | cmraJnt_v1.2 | 1 |
| CPU bracket | 3.0 | cpuBrkt_v3.0 | 1 |
| Kickstand | 1.4 | kickStnd_v1.4 | 1 |
| motor driver bracket | 1.5 | mDrvBrkt_v1.5 | 1 |
| twist bracket | 3.2 | twistBrkt_v3.2  | 1 |
| wheel bracket L | 1.5 | wheelBrktL_v1.5 | 1 |
| Wheel bracket R | 1.5 | wheelBrktR_v1.5 | 1 |
| Wrench | 2.0 | wrench_v2.0 | 1 |
| Serial tag | 1.0 | serialTg_v1.0 | 1 |

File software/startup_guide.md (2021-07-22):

## Examples

### INA
* has instruction: plug vs unplug power to the battery & measure the voltage
* uses INA219
* does not need NodeRed flow
* Needs a slide for wiring updated (DM)

### Gamepad
* start with flow from prior examples
* Learning:
  * joystick axes outputs and ranges
  * EITHER movement of xd, td (preferred) OR wheel speeds (needs a reason)
  * indicator for 1 button (y-button)
  * NO encoders

### SERVO
* on hold for DM - write the L1 file
* Needs a slide for wiring connections (DM)
* does NOT need nodeRed
* Steps: download file, hookup, verify direction (left, right), verify angle

### ENCODER
* need to write a nodered flow including chart (2 values, 1 chart)
* L1 encoder --> L2_myEncoderExampleName --> nodered
* L1 log --> L2_myEncoderExampleName
* indicate the programs structure in a slide

### CAMERA
* Verify nominal values for radius/pixels (too far, too close)
* Update slide in software guide based on nominal values (DM)
* 

## STEPS

### Downloading Image
  * DM to set up a link on scuttlerobot.org

### Location of Flows
  * flows belong in SCUTTLE/software/nodered
  * name should be descriptive of the contents, not the module
  * should have .json file extension

## Nodered
  * do we have the dashboard Widgets installed straight from the image? (READY 7.21)

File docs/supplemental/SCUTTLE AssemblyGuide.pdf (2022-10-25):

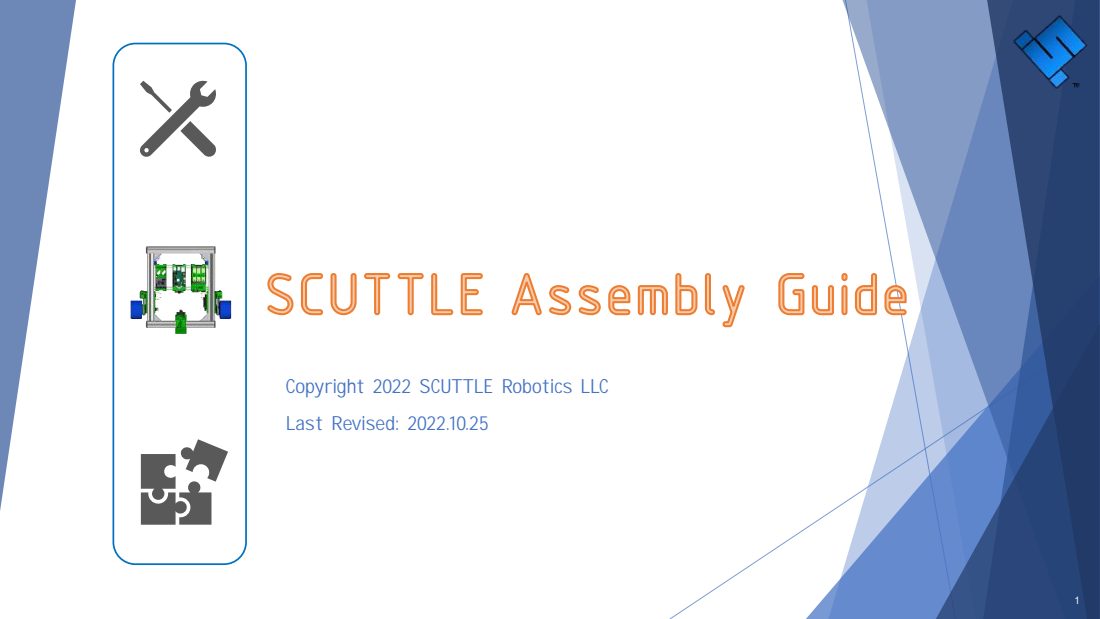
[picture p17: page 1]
Last Revised: 2022.10.25

Copyright 2022 SCUTTLE Robotics LLC

# In This Guide:

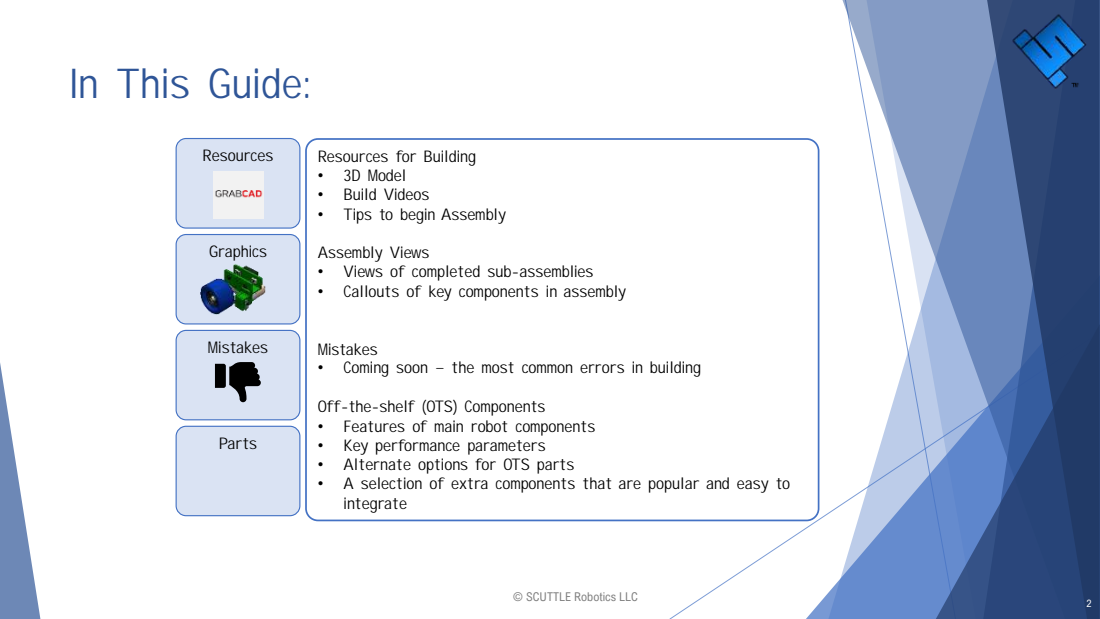
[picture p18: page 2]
Graphics; Resources; Mistakes; Parts

Resources for Building
• 3D Model
• Build Videos
• Tips to begin Assembly

Assembly Views
• Views of completed sub-assemblies
• Callouts of key components in assembly

Mistakes
• Coming soon – the most common errors in building

Off-the-shelf (OTS) Components
• Features of main robot components
• Key performance parameters
• Alternate options for OTS parts
• A selection of extra components that are popular and easy to
integrate

© SCUTTLE Robotics LLC

# SCUTTLE Assembly Tip:

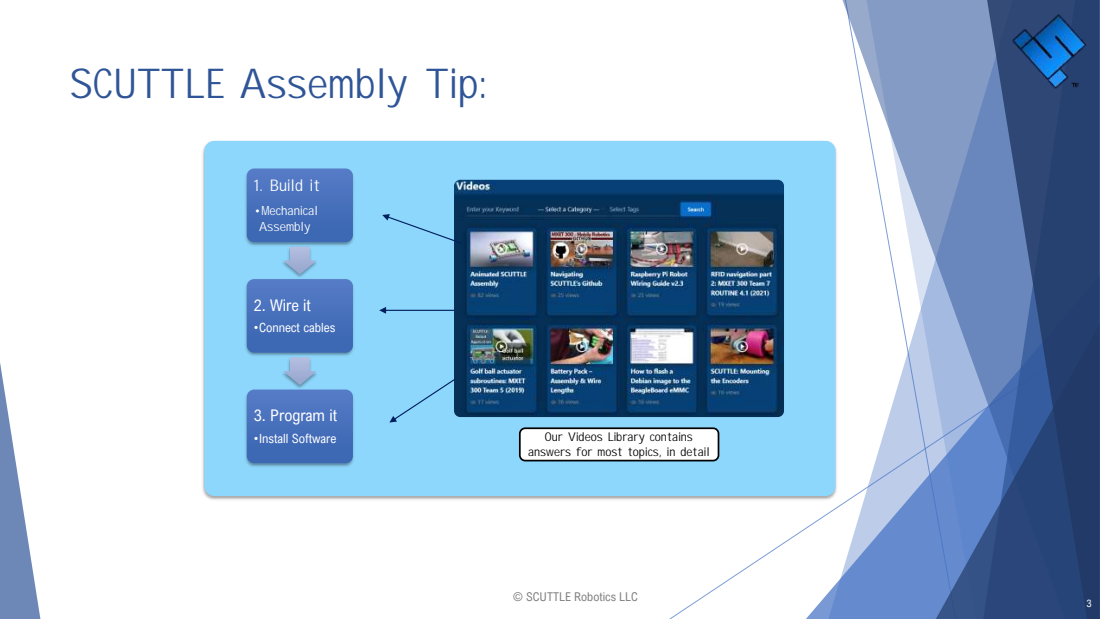
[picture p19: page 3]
1. Build it; •Mechanical Assembly; 2. Wire it; •Connect cables; 3. Program it; •Install Software

Our Videos Library contains
answers for most topics, in detail

# 3D Assembly Model

1

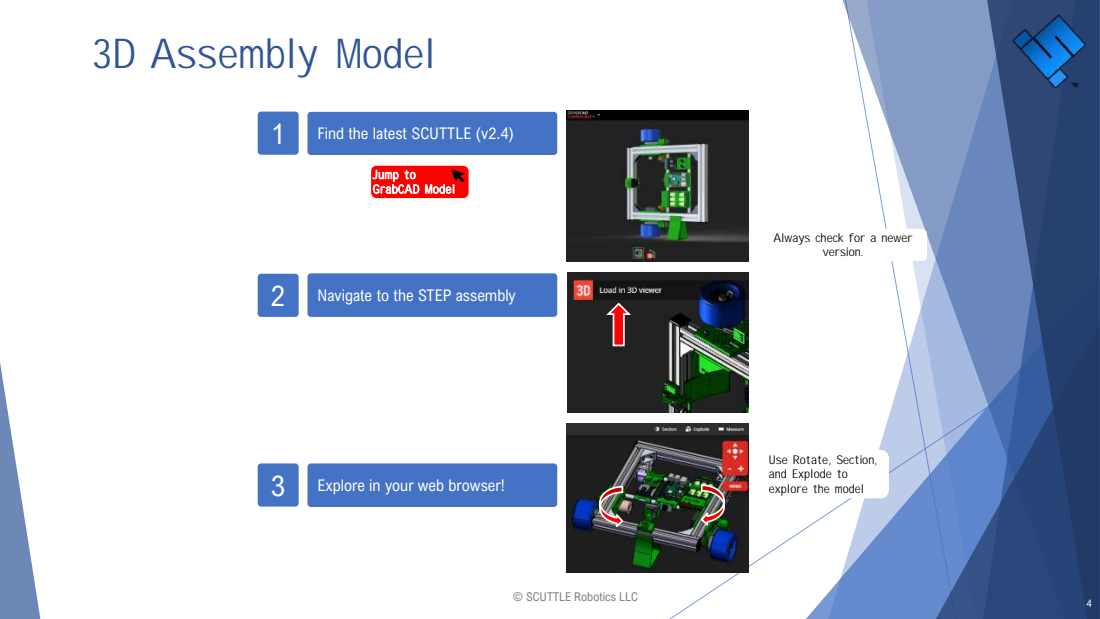
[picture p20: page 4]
version.; Jump to GrabCAD Model

Find the latest SCUTTLE (v2.4)

Always check for a newer

Navigate to the STEP assembly

Use Rotate, Section,
and Explode to
explore the model

Explore in your web browser!

# Build Videos

### The best videos to get

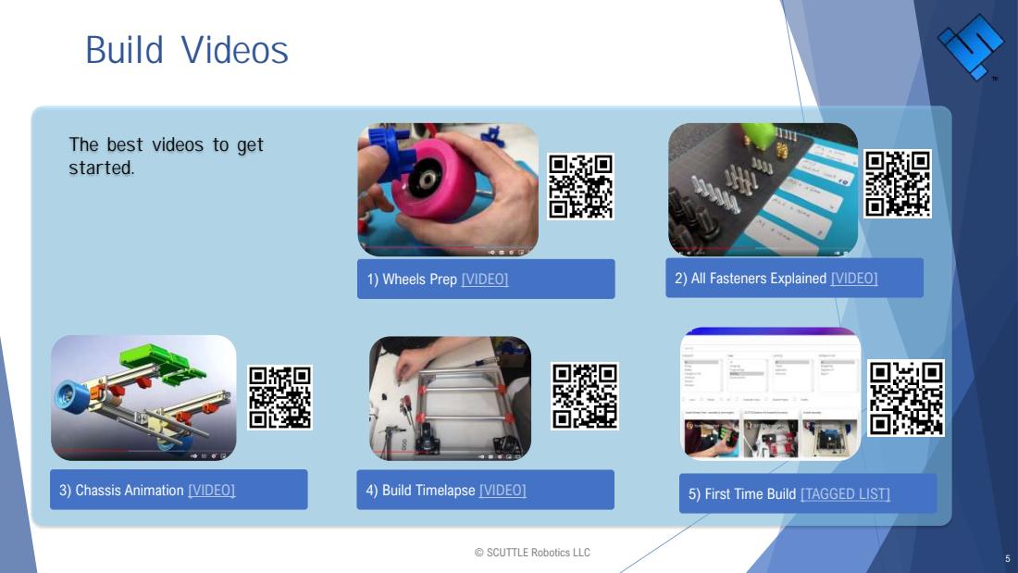
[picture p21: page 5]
4) Build Timelapse [VIDEO]; 5) First Time Build [TAGGED LIST]; started.

1) Wheels Prep [VIDEO] (https://www.scuttlerobot.org/aiovg_videos/press-in-the-wheel-bearings-glue-wheel-pulleys/)

2) All Fasteners Explained [VIDEO] (https://www.scuttlerobot.org/aiovg_videos/scuttle-robot-hardware-list-fasteners-screws-nuts-washers/)

3) Chassis Animation [VIDEO] (https://www.youtube.com/playlist?list=PLHkrnCQ5sDmdyelgZAIN76-Y_Tug1E4Ug)

# Assembly Sequence

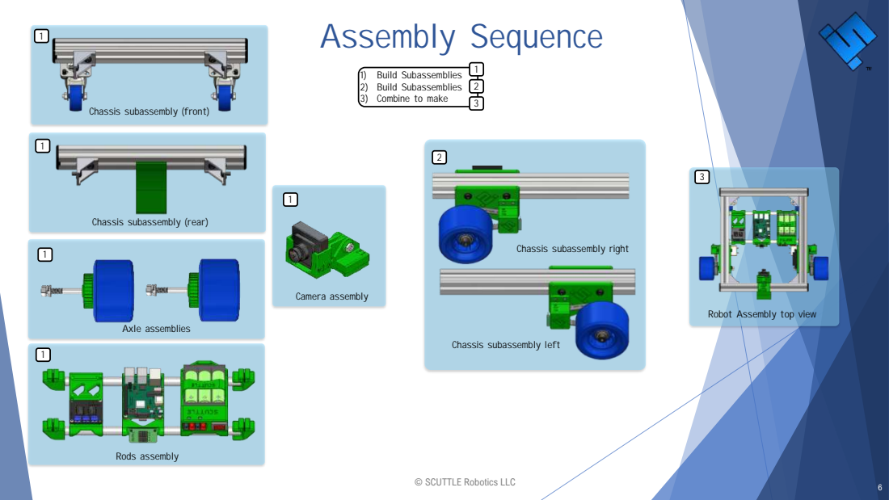
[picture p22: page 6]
Axle assemblies; Rods assembly; Camera assembly

1) Build Subassemblies
2) Build Subassemblies
3) Combine to make

Chassis subassembly (front)

Chassis subassembly (rear)

Chassis subassembly right

Robot Assembly top view

Chassis subassembly left

# Rods Assembly

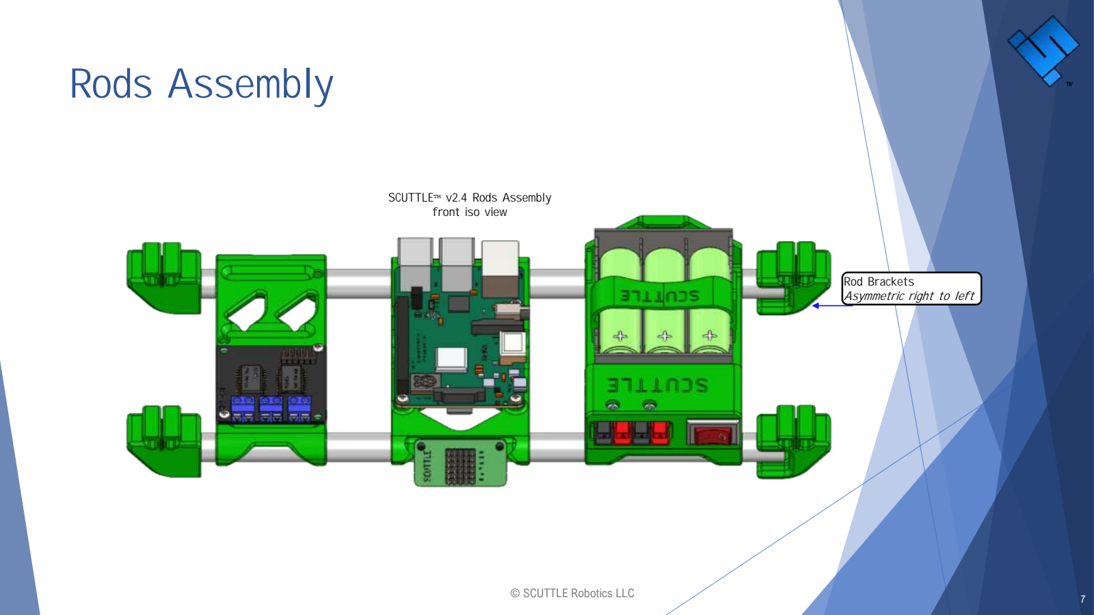
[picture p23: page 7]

Rod Brackets
Asymmetric right to left

SCUTTLE™ v2.4 Rods Assembly front iso view

# Camera Assembly

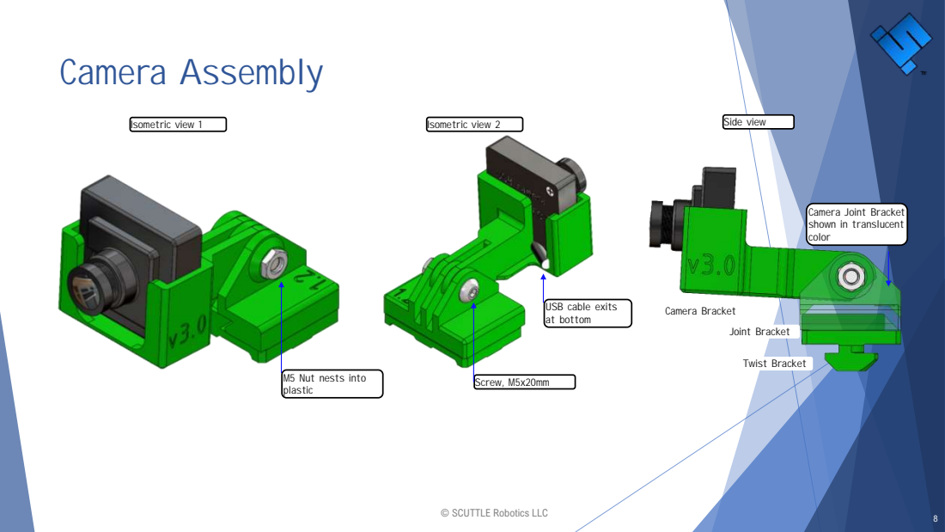
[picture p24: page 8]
Isometric view 1; Side view; Twist Bracket; Joint Bracket; Camera Bracket; Isometric view 2; Screw, M5x20mm

Camera Joint Bracket
shown in translucent
color

USB cable exits
at bottom

M5 Nut nests into
plastic

# Axle Assembly

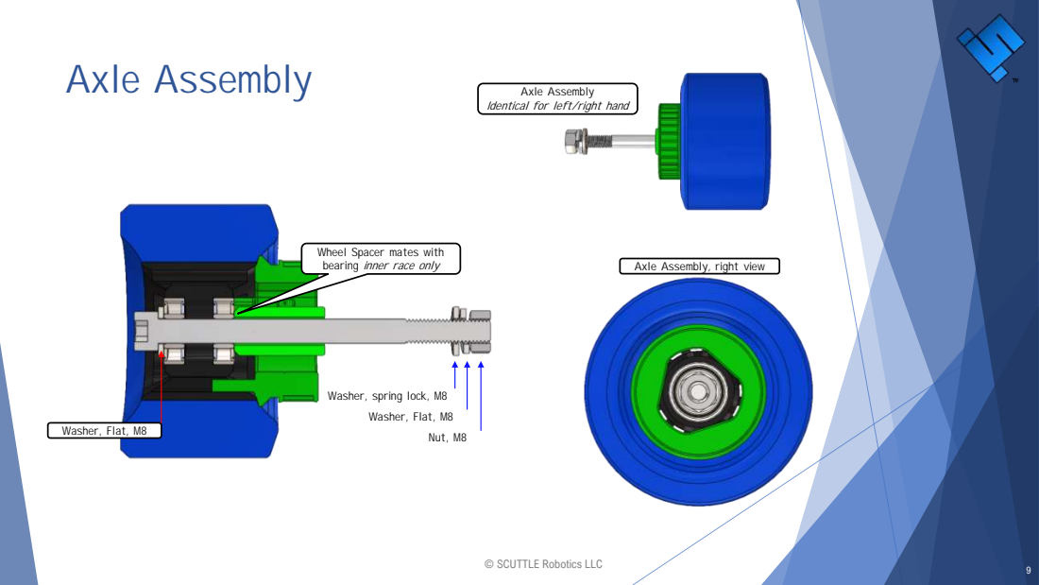
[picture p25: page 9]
Axle Assembly; Nut, M8; Washer, Flat, M8; bearing inner race only; Axle Assembly, right view

Identical for left/right hand

Wheel Spacer mates with

Washer, spring lock, M8

# Wheel Assembly

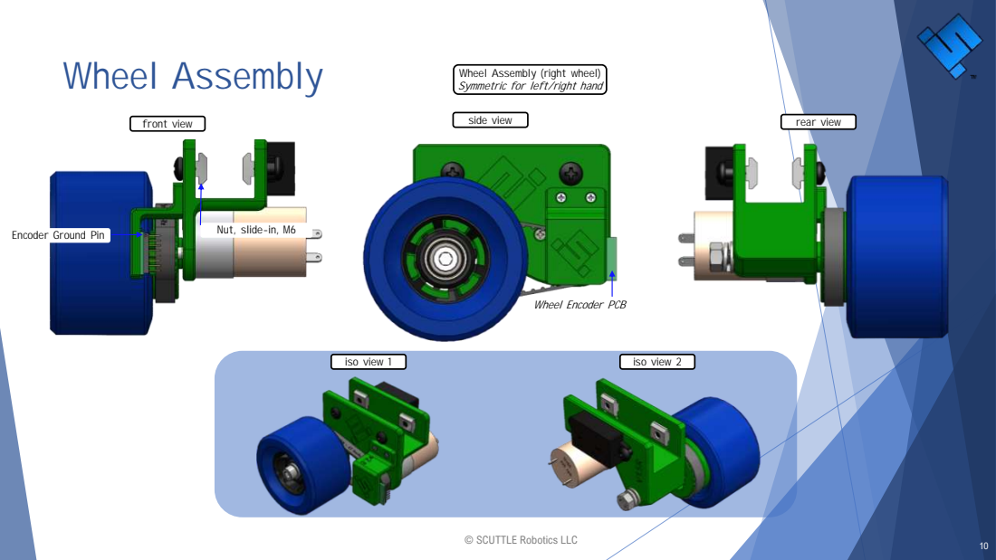
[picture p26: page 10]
front view; side view; rear view; iso view 1; iso view 2

Wheel Assembly (right wheel)
Symmetric for left/right hand

Nut, slide-in, M6

Encoder Ground Pin

Wheel Encoder PCB

# Chassis Subassemblies

Front Subassembly | Rear Subassembly

Kickstand

End Caps | Screw, M6x12
| Screw, M6x12

# Robot Assembly

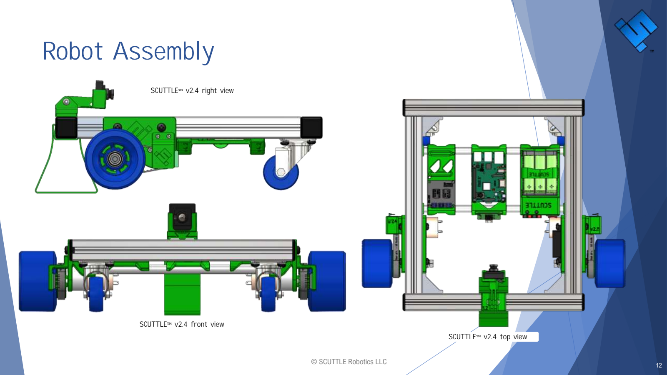
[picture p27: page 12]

SCUTTLE™ v2.4 right view

SCUTTLE™ v2.4 front view

SCUTTLE™ v2.4 top view

# Assembly Check List

### - Front Caster has clearance to rotate 360 degrees

### - Camera bracket seats on camera pivot without sliding off

### - Electronics

- Sequenced by Battery, CPU, Motor Driver (right to left)

### - Chassis

- End-caps (4) fit snugly or have hot glue to remain fixed
- Chassis flatness is achieved (extrusions lie on same plane)
- Extrusion faces touch their perpendicular mating extrusions (no gap)

### - Wheel Assemblies

- Belt is aligned parallel to outside face of wheel bracket
- M8 hex nut is only tight enough to flatten the lock-washer (no further)
- Both wheels can be rotated by hand with equal torque (both wheels, both directions)

### - Battery

### - Fasteners

- For M6 fasteners: slide-in nuts are used in wheel brackets while drop-in nuts are used elsewhere.

# SCUTTLE Revision Numbers

Next, follow our youtube videos (it’s a Item CAD Assembly •Latest: on GrabCAD •CAD Assembly Version •New version contains the latest native | | playlist, NOT A CHANNEL) | •Latest: on gitHub •Parts version 1.x, 2.x, •Means significant shape change before the | STL Files | •Latest: on grabCAD •Within Assembly or •Standalone subassembly | Example of this kind of revision CAD components
Robot assembly, major Solidworks geometry •Change from V2.2 to V2.3 has mostly compatible parts •Change from V2 to V3 means major design | vX.x | ❌ | grabCAD decimal •After decimal, compatibility) | 🏀 minor shape change (keeps | SLDASM, •By request only •V1.0 or V2.0 not related to grabCAD STEP assembly | Changed robot construction. To use wheel brackets instead of assembly of plates.
Robot assembly, minor change – not compatible | vX.x | ✔️ | grabCAD | 🏀🏀 | •Changes SLDASM, •Improved printing STEP •Improved identification •Improved fitment | v1.1 to v1.2 relate to: Many minor improvements on the modeling but not the design function
3D printed part, major | vX.x | ❌ | gitHub | 🏀🏀 | STL •Improved clearances •Maintain compatibility | Changed a bracket design to a new shape. Does not fit in place of the old part.
3D printed part, minor | vX.x | ✔️ | gitHub | 🏀🏀🏀🏀🏀 | STL | Improved a bracket for printability or clearances. Still fits in old part assembly.
OTS part | None | ✔️ | by request | 🏀🏀🏀 | SLDPRT, STEP | Designed a new CAD model to reflect hardware measurements
Subassembly, major | vX.x | ❌ | grabCAD | 🏀🏀 | | Tested a new kind of camera and sharing the model of a new camera & custom bracket. Not changing standard components.

Naming

Compatible

with previous?
Where to find
Frequency of

updates
Format

# Motor: DC gearmotor, 200rpm

Scuttle has two motors for driving the rear wheels. Each is a 12v DC motor with a gearbox that reduces the output speed to 200 RPM. The 6mm shaft is offset by 7mm from the centerline of the motor, which helps raise the clearance of the motor housing from the ground in the robot chassis. Three M3x10 screws fasten the motor to the motor plate.

The motor leads must be soldered to wires of 18 AWG or larger.

12v dc motor
with gearbox

Alternates: you can find other versions of this motor with different speeds. The 250RPM version, has higher speed and lower torque.

Converting to brushless is an exciting option but it requires both hardware and software adaptations, and higher cost.

Front face
drawing

# Motor Specs:

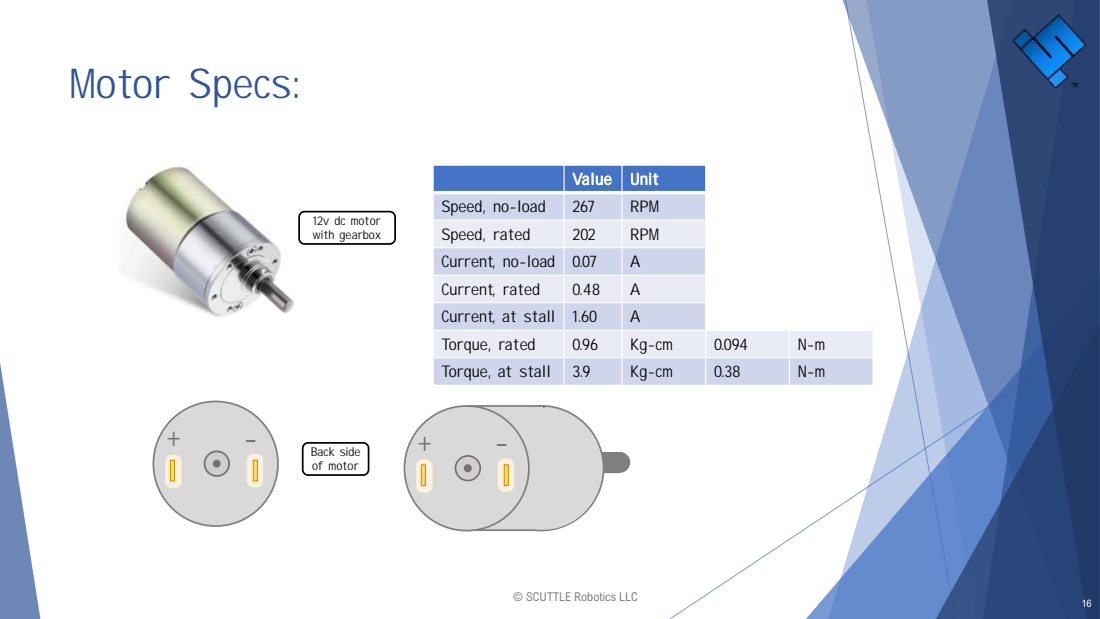
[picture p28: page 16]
12v dc motor with gearbox; Back side; of motor

Value | Unit

Speed, no-load | 267 | RPM
Speed, rated | 202 | RPM
Current, no-load | 0.07 | A
Current, rated | 0.48 | A
Current, at stall | 1.60 | A
Torque, rated | 0.96 | Kg-cm | 0.094 | N-m
Torque, at stall | 3.9 | Kg-cm | 0.38 | N-m

# Belt & Pulleys: HTD5 and T5

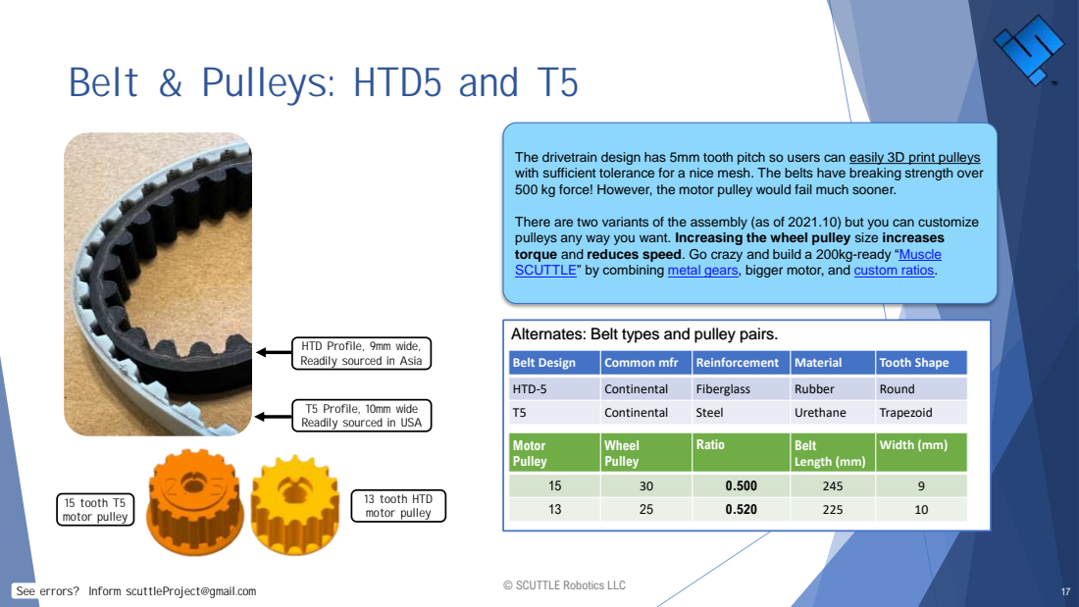
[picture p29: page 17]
13 tooth HTD motor pulley; 15 tooth T5 motor pulley

The drivetrain design has 5mm tooth pitch so users can easily 3D print pulleys
with sufficient tolerance for a nice mesh. The belts have breaking strength over
500 kg force! However, the motor pulley would fail much sooner.

There are two variants of the assembly (as of 2021.10) but you can customize
pulleys any way you want. Increasing the wheel pulley size increases
torque and reduces speed. Go crazy and build a 200kg-ready “Muscle
SCUTTLE” by combining metal gears, bigger motor, and custom ratios. (https://youtu.be/-C9X-VSfA-4)

Alternates: Belt types and pulley pairs.

HTD Profile, 9mm wide,
Readily sourced in Asia

Belt Design | Common mfr | Reinforcement | Material | Tooth Shape

HTD-5 | Continental | Fiberglass | Rubber | Round
T5 | Continental | Steel | Urethane | Trapezoid

T5 Profile, 10mm wide
Readily sourced in USA

Motor Pulley | Wheel Pulley | Ratio | Belt Length (mm) | Width (mm)

15 | 30 | 0.500 | 245 | 9
13 | 25 | 0.520 | 225 | 10

See errors? Inform scuttleProject@gmail.com

# Embedded Computer – Beaglebone Blue

The beaglebone Blue is an embedded Linux computer with extra robotics features such as built in motor drivers and dual WiFi modules, power management and servo ports.

More resources:
Beaglebone Blue Wiki (https://github.com/beagleboard/beaglebone-blue/wiki)
Beaglebone Blue Specification Sheet (https://github.com/beagleboard/beaglebone-blue/blob/master/docs/BeagleBone_Blue_ShortSpec.pdf) Beaglebone Blue Schematic (https://github.com/beagleboard/beaglebone-blue/blob/master/BeagleBone_Blue_sch.pdf)
Summary Video (https://youtu.be/IJIgCd02Atg?list=PLHkrnCQ5sDmdyelgZAIN76-Y_Tug1E4Ug) in 1 Minute

Beaglebone Blue

Alternates: you can also use Raspberry Pi or other single board computer (SBC).

Other modules will require separate purchase of:
- Power regulator
- 2

nd Wifi Dongle
- Servo driver (if used)

# Embedded Computer – Raspberry Pi 4

Raspberry Pi is the top-selling embedded Linux computer, with higher computing performance but it lacks onboard modules compared with the Beagle (LiPo charger, PWM generators, secondary WiFi module) and it requires a regulated power input. Pi is the standard as of SCUTTLE v2.3 for the kit offering. SCUTTLE software is tested on Pi v3B and forward.

More resources:
Raspberry Pi website (https://www.raspberrypi.org/)
Raspberry Pi pin diagram at pinout.xyz Raspberry Pi 4 v1.2 sold at mouser.com (https://www.mouser.com/ProductDetail/Seeed-Studio/102991317?qs=OlC7AqGiEDmfbSblMUfeqg%3D%3D) Raspberry Pi 4 datasheet (https://www.mouser.com/datasheet/2/744/Raspberry_Pi_4_Product_Brief-2507283.pdf)

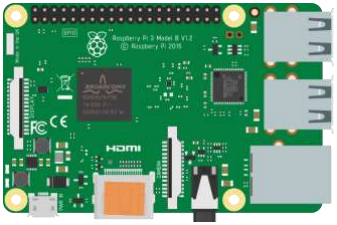
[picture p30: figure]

Raspberry Pi (model 3 shown) Key Features:
•ARM Processor—quad-core @1.5Ghz for model 4 •Connectivity— onboard WiFi transciever
•Memory— LPDDR4 (2 gigabytes selection)
•Hard disc—uses the user-selected SD card for hard drive, (32gb Samsung Evo Select is standard)
•Input Power--5v DC, minimum 3A

# Embedded Computer – TI TDA4VM Board

The Edge AI Starter Kit (SK) board with TDA4VM Processor leaps into deep learning territory with 8 Tera Operations Per Second (TOPS) and is specialized for realtime processing of up to 8 camera inputs and multiple.

More resources:
SCUTTLErobot.org Partner Page (https://scuttlerobot.org/ti)
Edge AI Robotics Academy (https://dev.ti.com/tirex/content/robo_academy_0_00_00_01_eng__all/landing_page.html)
Edge AI Starter Kit Product Page (https://www.ti.com/tool/SK-TDA4VM) ($249 USD) Unboxing and Starting Video (https://training.ti.com/sk-tda4vm-8-tops-deep-learning-starter-kit-edge-ai-application-development)
TI/Robotics software Quick Start (https://software-dl.ti.com/jacinto7/esd/robotics-sdk/08_02_00/docs/index.html)

TDA4VM-based Edge AI SK Board

Key Features:
•Camera interfaces—two CSI-2 ports compatible with Raspberry Pi and a high-speed 40-pin Semtec camera connector connecting up to eight cameras (requires TIDA-01413 sensor fusion add-on card) •Connectivity—three USB 3.0 Type A ports, one USB 3.0 Type C ports, one ethernet port, one M.2 Key E connector and one M.2 Key M connector, four CAN-FD interfaces, four UART terminals over one USB bridge •Memory—DRAM, LPDDR4‐4266, 4 gigabytes total memory, support for inline ECC
•Display—DisplayPort with up to 4K resolution with MST support and 1080 HDMI

# Encoders

Two AMS AS5048B encoders are required for SCUTTLE, with one at each motor pulley.

Some details:
- It’s actually an angular position sensor. It returns degrees, from 0 to 360.
- It communicates over I2C. The left-hand encoder is addressed as 0x40 and the Right-hand encoder is addressed as 0x41, assigned by address pins.
- They measure the rotation of the motor pulley, and the software adjusts for (approx 1:2) wheel:motor turn ratio
- The sensor is paired with a diametrically opposed magnet, mounted at the end of the motor shaft.

Resources for the encoder:
AMS AS5048B Datasheet (https://www.mouser.com/ds/2/588/AS5048_DS000298_3-00-522570.pdf)

ASM AS5048B
Encoder PCB

The encoder addresses are set by soldering and wiring according to our wiring diagrams.

Pin A0 | Pin A1 | Resulting i2c address
Left Encoder | LOW | HIGH | 0x41
Right Encoder | LOW | LOW | 0x40

# Dual Motor Driver

A number of motor driver options are available. The standard choice is HW-231 motor driver which uses the NXP MC3386 H-Bridge. The ground is connected directly to the battery pack and it accepts two input pin pairs as PWM channels.

Resources for the motor driver are here:

- MC3386 Datasheet (https://www.nxp.com/docs/en/data-sheet/MC33886.pdf)

Motor Driver
with dual MC33886 | Alternate: the ever-common L298N will also work for driving the
| motors, but it will not drive enough current for full output of our
| motors. It’s an option if you’re just learning and want to save
| money.
| Important Features:
| • Board is available from array of unbranded distributors with
| genuine FETs.
| • Drives up to 5A per channel, continuously.
| • Up to 10KHz PWM frequency
| • 5.0 to 40.0v operation

# Battery Pack

The battery pack is a 3-cell lithium ion pack with a nominal voltage of 11.1v (3.7v per cell) combined with a few off-the-shelf parts and a 3D printed case. The capacity is 3400 mAh (we verified!) And they have enough capacity to drive SCUTTLE for several hours.

With additional actuators, a significant payload, or
demanding sensors such as the SICK LIDAR, it is advised to add more capacity to the robot. The cells must not be drained below 2.8 volts each to prevent damage.

Resources for the battery pack are here:

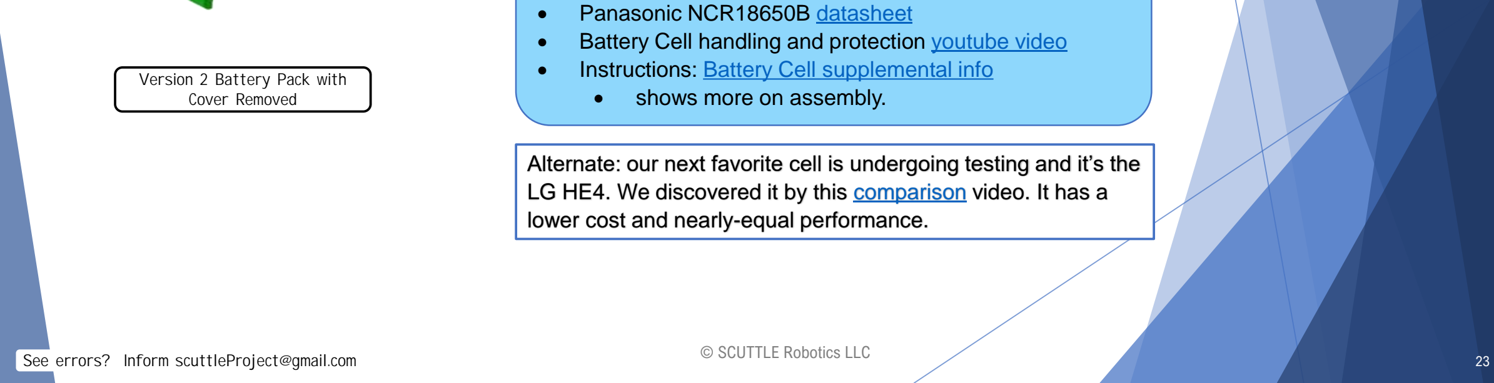
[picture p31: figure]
• Panasonic NCR18650B datasheet; • shows more on assembly.; Version 2 Battery Pack with Cover Removed; lower cost and nearly-equal performance.; See errors? Inform scuttleProject@gmail.com

- Battery Cell handling and protection youtube video (https://www.youtube.com/watch?v=fC4sgXplA3k&t=2s)
- Instructions: Battery Cell supplemental info (https://github.com/MXET/SCUTTLE/blob/master/docs/supplemental/Battery%20Pack%20Supplemental%20Info.pdf)

Alternate: our next favorite cell is undergoing testing and it’s the LG HE4. We discovered it by this comparison (https://youtu.be/qMZuHMlRw_0) video. It has a

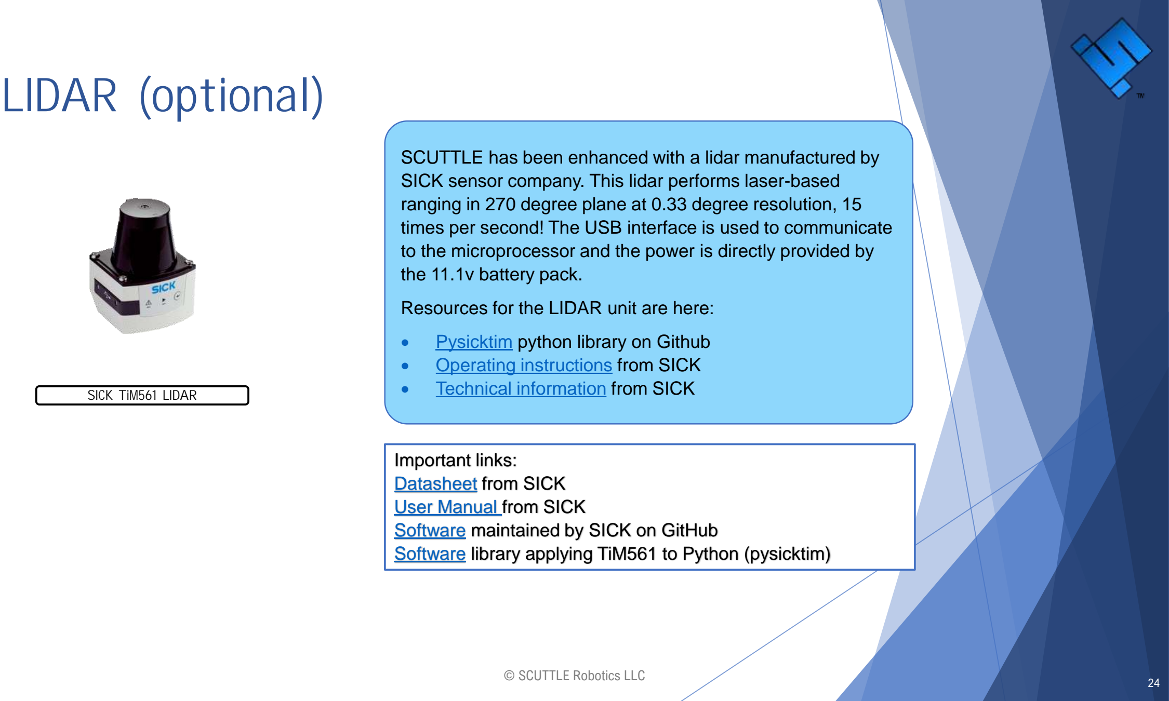
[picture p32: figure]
LIDAR (optional); the 11.1v battery pack.; Resources for the LIDAR unit are here:; • Pysicktim python library on Github • Operating instructions from SICK; SICK TiM561 LIDAR; Technical information from SICK; Important links: Datasheet from SICK User Manual from SICK Software maintained by SICK on GitHub

SCUTTLE has been enhanced with a lidar manufactured by SICK sensor company. This lidar performs laser-based ranging in 270 degree plane at 0.33 degree resolution, 15 times per second! The USB interface is used to communicate to the microprocessor and the power is directly provided by

Software (https://github.com/ansarid/pysicktim) library applying TiM561 to Python (pysicktim)

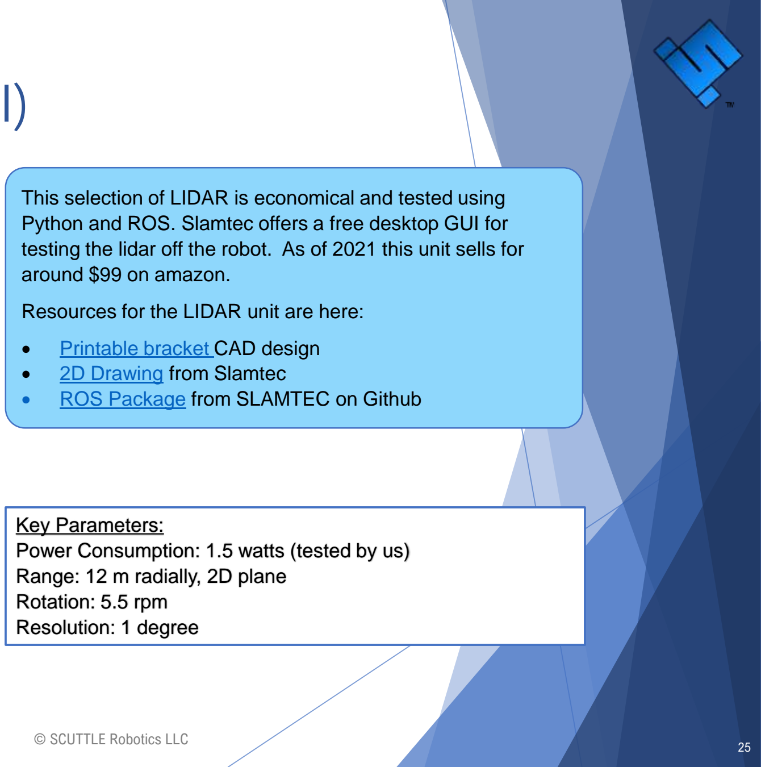
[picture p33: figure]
around $99 on amazon.; Resources for the LIDAR unit are here:; • Printable bracket CAD design • 2D Drawing from Slamtec • ROS Package from SLAMTEC on Github; Key Parameters:; Range: 12 m radially, 2D plane Rotation: 5.5 rpm Resolution: 1 degree

# LIDAR (Preferred Model)

This selection of LIDAR is economical and tested using Python and ROS. Slamtec offers a free desktop GUI for testing the lidar off the robot. As of 2021 this unit sells for

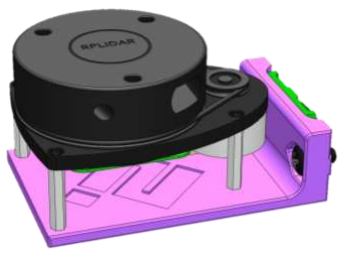
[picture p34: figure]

RPLIDAR A1 with Bracket

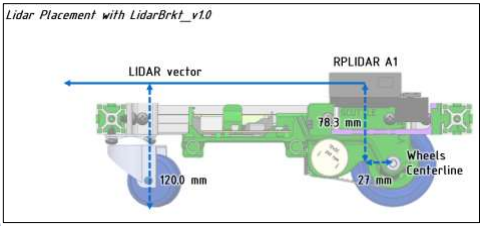
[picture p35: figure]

Power Consumption: 1.5 watts (tested by us)

# LIDAR (continued)

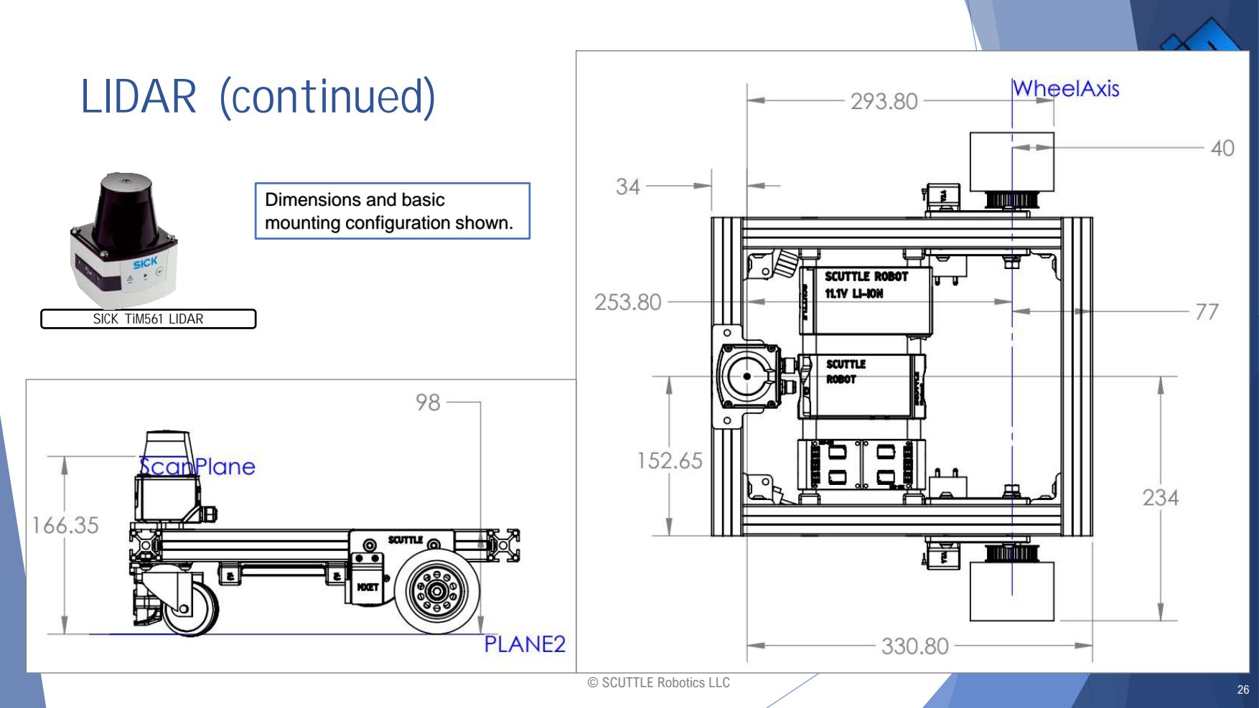
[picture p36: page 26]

SICK TiM561 LIDAR

Dimensions and basic
mounting configuration shown.

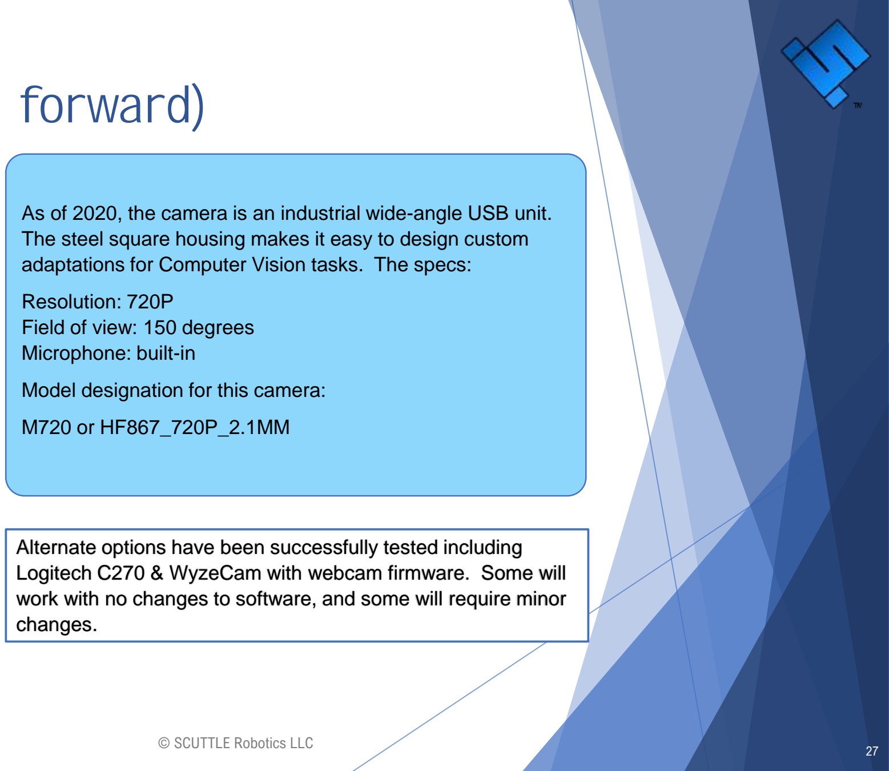
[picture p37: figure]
Resolution: 720P Field of view: 150 degrees Microphone: built-in; Model designation for this camera:; changes.

# USB Camera (v2.3 forward)

As of 2020, the camera is an industrial wide-angle USB unit. The steel square housing makes it easy to design custom adaptations for Computer Vision tasks. The specs:

M720 model USB Camera | Alternate options have been successfully tested including Logitech C270 & WyzeCam with webcam firmware. Some will work with no changes to software, and some will require minor

# Time-of-Flight (ToF) Sensor

The ToF sensor uses a light beam to measure distances to the nearest surface.

This sensor is ultra-low power, highly repeatable, and low cost. It uses i2c protocol, a big advantage over the ultrasonic option.

The key functional difference between this sensor and the ultrasonic sensor is the directionality of the beam.

Resources for the HC-SR04 are here:

VL53L0X on Amazon (https://www.amazon.com/Organizer-VL53L0X-Breakout-GY-VL53L0XV2-Distance/dp/B07XXTMRR2) ($12.99 for 2pcs) VL53L0X on Adafruit (https://www.adafruit.com/product/3317) (with tutorials) Fantastic details in the Datasheet (http://www.st.com/content/ccc/resource/technical/document/datasheet/group3/b2/1e/33/77/c6/92/47/6b/DM00279086/files/DM00279086.pdf/jcr:content/translations/en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)

VL53L0X ToF Sensor

Specs:
- Operates on 3.3 or 5.0v
- typical sensing range [50mm to 1200mm]
- typical accuracy of 7% of measurement
- typical sensing time, 30ms (33 per second!)
- repeatability around 5% of measurement Detection range pattern

# Ultrasonic Sensor

The ultrasonic sensor is for range-finding. It’s an optional item to support autonomous driving and obstacle avoidance.

There are versions of this board which require 5v (more common) or only 3.3v (less common). If your board requires 5.0v then power will need to be drawn directly from the power port on the beaglebone.

Resources for the HC-SR04 are here:

HC-SR04 Datasheet (https://cdn.sparkfun.com/datasheets/Sensors/Proximity/HCSR04.pdf)

HC-SR04 Ultrasonic
Ranging Sensor

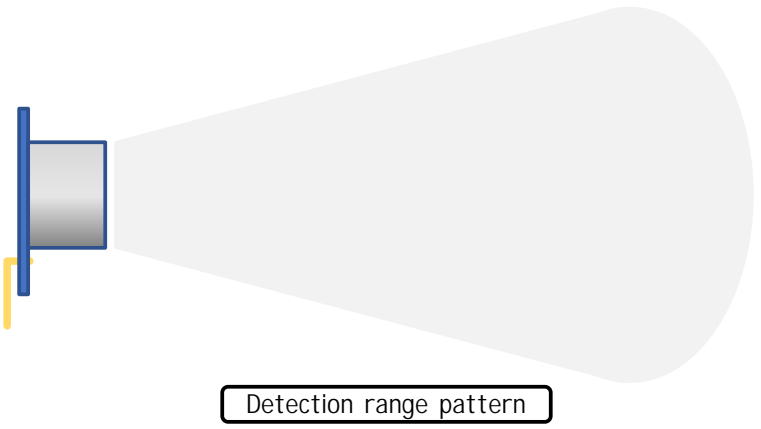
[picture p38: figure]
Detection range pattern

Alternate options include ToF sensors, IR rangefinders, or full-on LIDAR. Both have been successfully tested.

# Power Connector

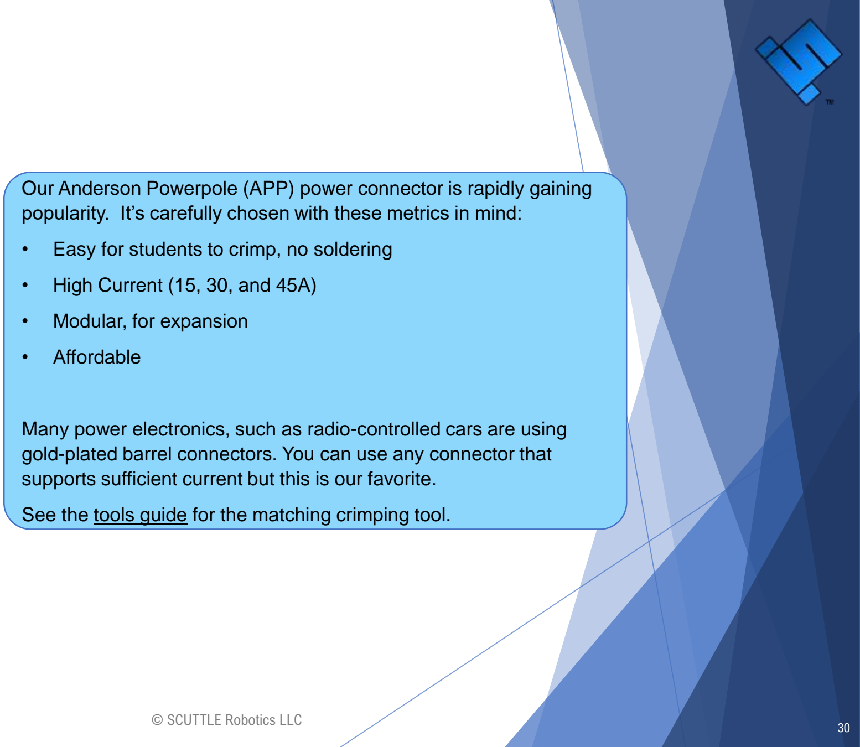
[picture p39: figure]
• High Current (15, 30, and 45A); • Modular, for expansion; • Affordable

Our Anderson Powerpole (APP) power connector is rapidly gaining popularity. It’s carefully chosen with these metrics in mind:

- Easy for students to crimp, no soldering

Many power electronics, such as radio-controlled cars are using gold-plated barrel connectors. You can use any connector that supports sufficient current but this is our favorite.

See the tools guide (https://www.scuttlerobot.org/resources/) for the matching crimping tool.

Anderson Powerpole
Connector Housings

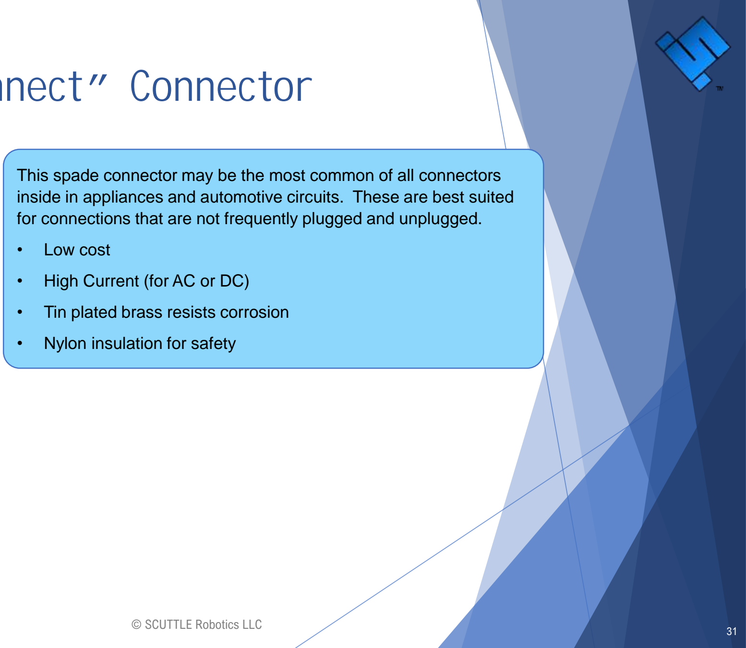
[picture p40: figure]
• Low cost; • High Current (for AC or DC); • Tin plated brass resists corrosion; • Nylon insulation for safety

# Spade “Quick Connect” Connector

This spade connector may be the most common of all connectors inside in appliances and automotive circuits. These are best suited for connections that are not frequently plugged and unplugged.

Spade Quick Connect
Terminal

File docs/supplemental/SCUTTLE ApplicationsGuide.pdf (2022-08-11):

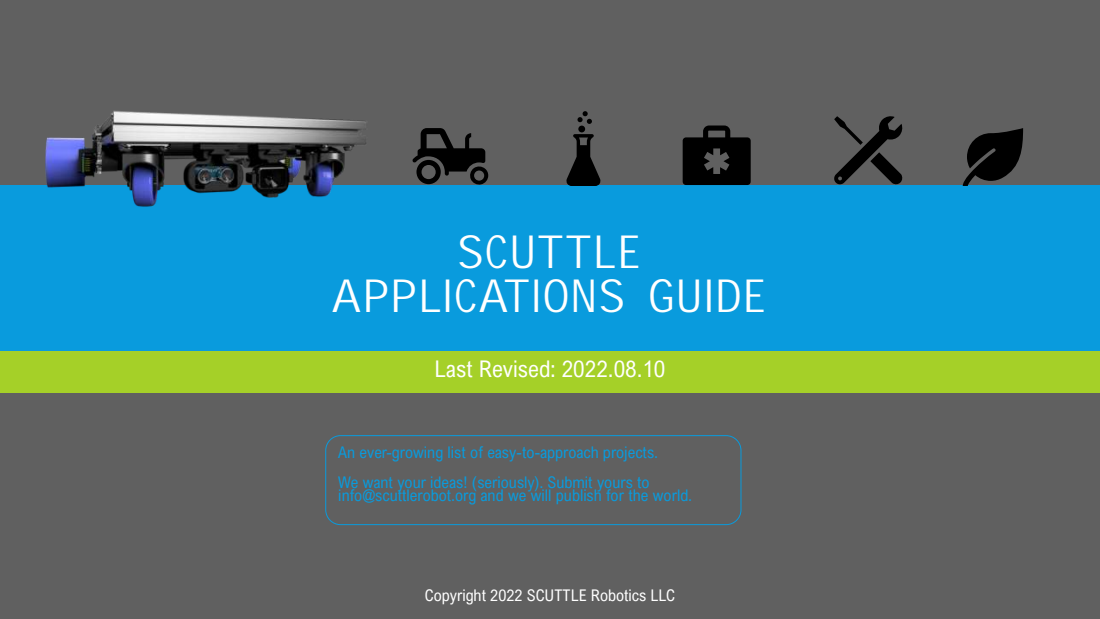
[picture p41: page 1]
SCUTTLE APPLICATIONS GUIDE; Last Revised: 2022.08.10

An ever-growing list of easy-to-approach projects.

We want your ideas! (seriously). Submit yours to
info@scuttlerobot.org and we will publish for the world.

Copyright 2022 SCUTTLE Robotics LLC

# IDEATION MINDSET

Project ideation is not just a matter of creativity, it’s a serious challenge in problem-solving and
STRUCTURED brainstorming.

This skill takes years to develop. Here are some ideation guidelines that often make or break a final project demo.

[Applications Guide] © SCUTTLE Robotics LLC | 2

# PROJECT TOPICS: HARDWARE BASED

## Projects that require additional actuators

Feasible scope for MVP in less than 6 months

Limited to 1 or 2 actuators

Only actuators & sensors which have open-source libraries already

### Applications Guide SECTION 1

# 1.1 ENVIRONMENTAL SAMPLING (GREENHOUSE)

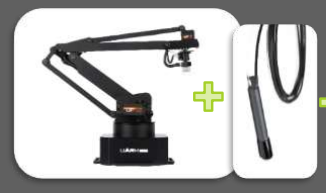
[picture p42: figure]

Task: Environmental measuring – Identify containers and probe for temp/moisture/pH

Why it’s Useful:
Currently, readings in these facilities are taken by people walking from point to point. Instead of sampling all regions, companies usually just take a few measurements, leaving the gradients to assumption. More thorough measurements will make more successful operations.

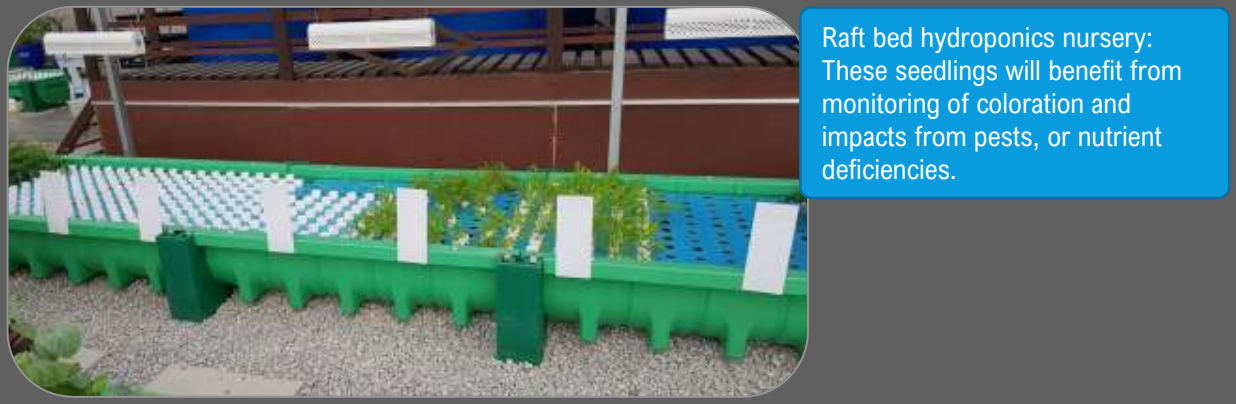
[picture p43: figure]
Raft bed hydroponics nursery: These seedlings will benefit from monitoring of coloration and impacts from pests, or nutrient deficiencies.

Why it is feasible:
Probes and their associated drivers can easily fit on a scuttle and within power budget. Probing for parameters does not require fine precision of movement so students can achieve this with basic software and materials.

# 1.2 SECURITY ROUTINE

Task: Security tasks – take photos of designated items & upload.

Why it’s useful:
Security guards can’t always catch subtle problems. When robots are added, photos can be taken in exact locations from day to day and image processing can run in the cloud to catch someone setting up for a theft.

Why it is feasible:
Camera and RFID technologies have already been tested on SCUTTLE with available examples.

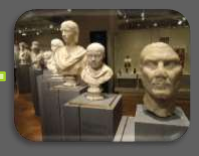
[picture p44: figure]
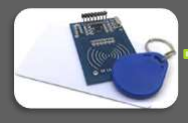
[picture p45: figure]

# 1.3 3D PRINTER FILAMENT HANDLING

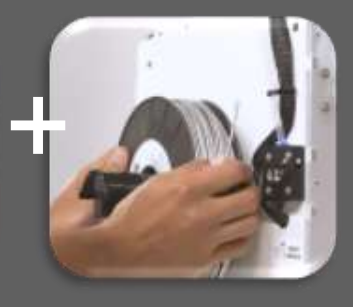
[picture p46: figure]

Task: Gather, transport, and load 3d filament spool onto hangers

Why it’s useful:
Many machines can nearly run autonomously except for the changing of filament. Filament loading gets the whole print factory one step closer to full autonomy.

Why it’s feasible:
Spools are standardized and found in most makerspaces. Low cost actuators don’t require additional power supply and have capability to lift or manipulate objects the size of spools.

# 1.4 MOBILE REFRESHMENTS

Task: Dispense purified water into cups where people need water.

Why it’s useful:
We don’t really know. All we know is that highly trained athletes are still getting assistance to drink water so why not help with a robot and spare some effort from the coach?

Why it is feasible: SCUTTLE has already shown ability to carry a full size water jug and more. 12v pumps are readily available and powerful enough to lift water at a reasonable rate.

# 1.5 RESTAURANT TABLE DELIVERY

Task:
- Carry trays of food or supplies to designated location.

Why it’s useful:
- tray delivery is a longstanding task for people. But since times of COVID-19, we aim to reduce the contact of waiters with dozens of people per hour.

Why it’s feasible:
- Trays have a standard and simple form factor. It’s just a matter of adding one light actuator to expel a tray when SCUTTLE reaches the destination table.

# 1.6 INVENTORY LABELING

Task: Add a portable label printer, identify boxes and label them with the proper information for shipping or contents.

Why it’s useful:

Inventory can change rapidly and accurate labeling is a need which exists across many industries.

Why it’s feasible:

New printing devices that print wirelessly have been on the market just for a short time. Their usefulness is enhanced when coupled to a machine which knows exactly it’s speed relative to the box to be printed on.

Example actuator:

- https://www.searchingc.com.my/products/printpe n

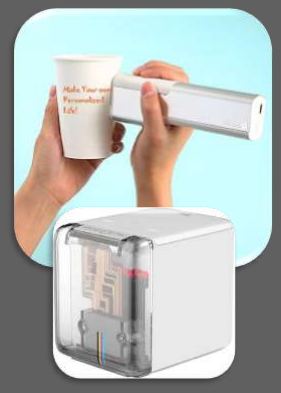
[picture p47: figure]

Youtube example: https://youtu.be/7Psmlwmv1fc

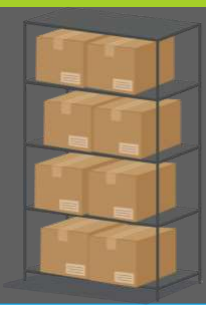
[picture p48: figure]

M-brush on amazon:
https://www.amazon.co.uk/Bluetooth-Printer-Portable-Cicarica-Anywhere/dp/B085VCRVS2

# 1.7 COLLECT TENNIS BALLS

Problem:

- Practicing tennis (or golf) can be inefficient since someone must collect the balls repeatedly.

Solution:

- Cruise around the court
- Detect balls by color & shape
- Collect them in a basket
- Bring to a designated spot & dump

# 1.8 PET STORE MONITORING

Problem:

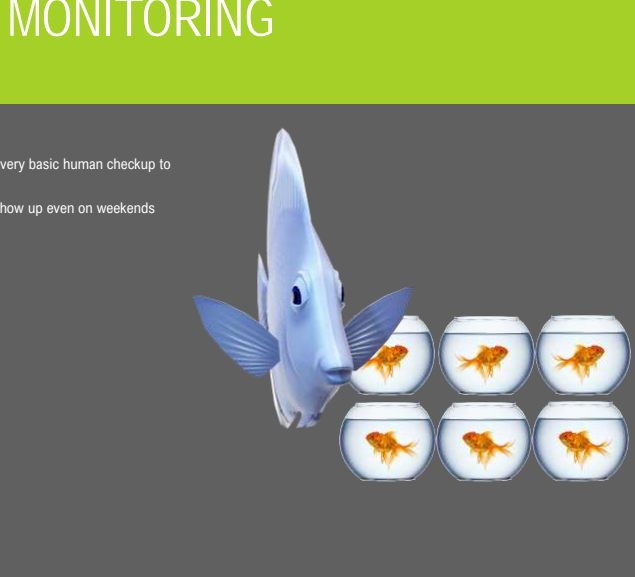
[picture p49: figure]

- Many stores carry living or sensitive items which need a very basic human checkup to avoid catastrophic losses.
- In laboratories in universities, undergrads are forced to show up even on weekends just to look at

Solution:

- Look after the pet store on holidays to give alerts
- For Dogs: detect barking in kennels
- For Fish: detect dead fish, or sample water
- pH
- Temp
- Salinity
- Etc
- For birds, reptiles, etc
- Customize programs for irregular behavior
- Sounds
- Violent motion (movement rate)
- Lack of motion or escape

# 1.9 HAZARD REPORTING

Problem:

- Each day, new hazards can show up in parks and public walks due to unexpected events.
- Trails are often closed after storms due to unknown hazards, until officials can review the condition.

Solution:

- Use Lidar to detect hazards to humans in the pathway
- Cracks in the sidewalk
- Debris
- Take a photo onsite to log the condition
- Send the photos instantly to officials by cell carrier
- Use GPS coordinates to send a report with photograph to the department who will make a repair or send a technician out for inspection.

# 1.10 THERMAL FACILITY AUDIT

Problem:

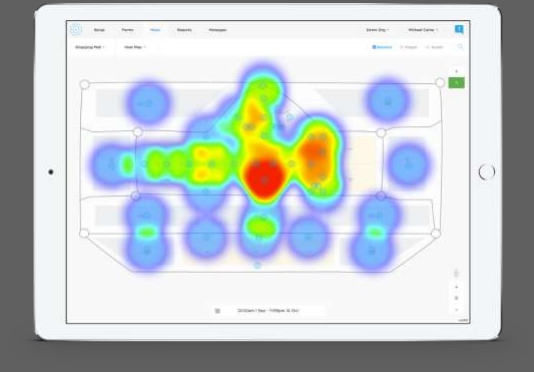
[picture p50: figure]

- Companies pay huge rates to make energy audits in their facilities.
- These audits must hire outside vendors because the outside vendors are trained in the necessary standards.

Solution:

- Train SCUTTLE with proper standards to audit buildings for thermal losses.
- Make a map of a building and take temperature measurements throughout
- Detect Windows & sources of airflow
- Use an air vane to detect airflow direction
- Generate a report on the indoor climate & areas of concern for heat buildup (cooling) and heat loss (heating)

# 1.11 FIRE FIGHTING BOT

Problem:

- Not everyone is capable and ready to manage a fire extinguisher (consider day cares, pets alone at home, or elderly care)

Solution:

- Employ a simple 2DOF arm for aiming an extinguishing nozzle.
- Payload: secure 1 or more fire extinguishers
- Optional: use thermal imaging to detect fires.

## Example Extinguisher

Product (amazon) (https://www.amazon.com/First-Alert-Extinguisher-Fire-Extinguisher-AUTO5/dp/B000P0DPGQ)

# 1.12 CAMPUS SECURITY ESCORT

- Universities have already identified a need for security during times when someone is alone or in need of help.

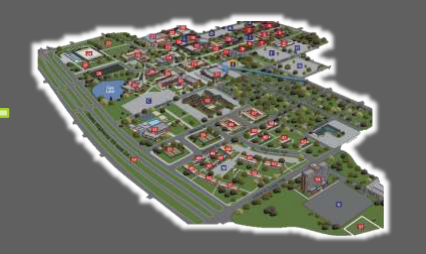
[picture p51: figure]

- A mobile security device is just an enhancement over fixed security call boxes.
- Budgets have already been allocated on this kind of infrastructure for many institutions.
- SCUTTLE can be equipped with emergency call functions, pathway lights for added safety or an extremely loud siren at the press of a button.
- Reliable 4G cellular modules are available off-the shelf to give redundant connectivity when wifi may be interrupted.

# 1.13 PROFESSIONAL POV PANORAMICS

Problem:
- panoramic photos are limited to single-POV execution, even for wide-spanning scenery.
- The ends of each panoramic lack the pixel density due to their distance from the camera

Solution:
- For taking pictures of malls, churches, riverside properties, etc. it is beneficial to take a new kind of panoramic.
- With updates to camera software, professional DSLR cameras can be activated to take a sweeping photo that is tied to the odometry of the wheels.
- Point and shoot: two simple servos can control a laser pointer which the camera person can use to indicate the extremities of a photo, upon which SCUTTLE will execute the image capture. Consider it like a flat-bed scanner but life-size.
- Dimensions and proportions can be more accurately captured for tagging of official measurements
- Also consider property planning for schools, bus stops, train stations, etc.

# 1.14 HIGH-VALUE VENDING MACHINE

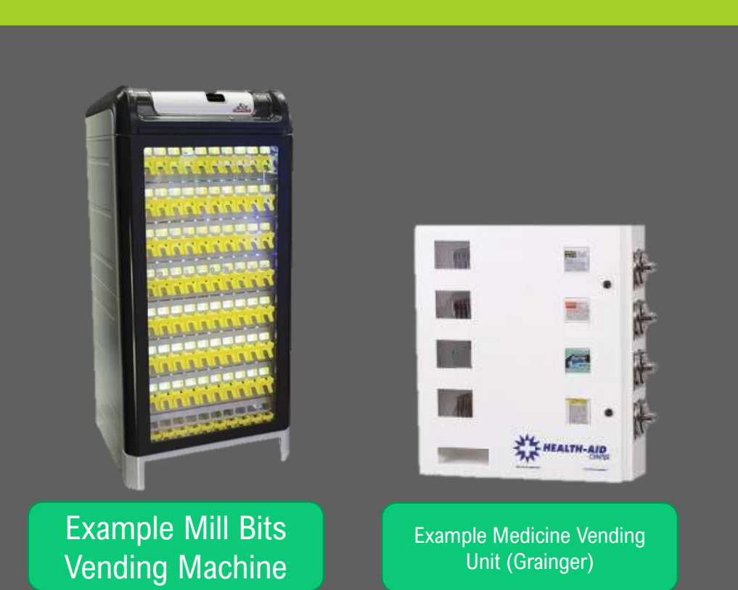
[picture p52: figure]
Example Mill Bits Vending Machine; Example Medicine Vending Unit (Grainger)

## Problem: - Manufacturing plants are many acres in size, and machinists must drive golf carts to a tools crib to check out expensive

components.

## - Other spaces like hospitals also carry

vending units that require security.

## - Automated tool cribs, which already exist, add security and efficiency to the

tool check-out process.

## Solution: - To make the process more efficient, we can combine the tool crib with autonomous driving to deliver parts based on an order, or a scanned RFID

# 1.15 CHARGING STATION

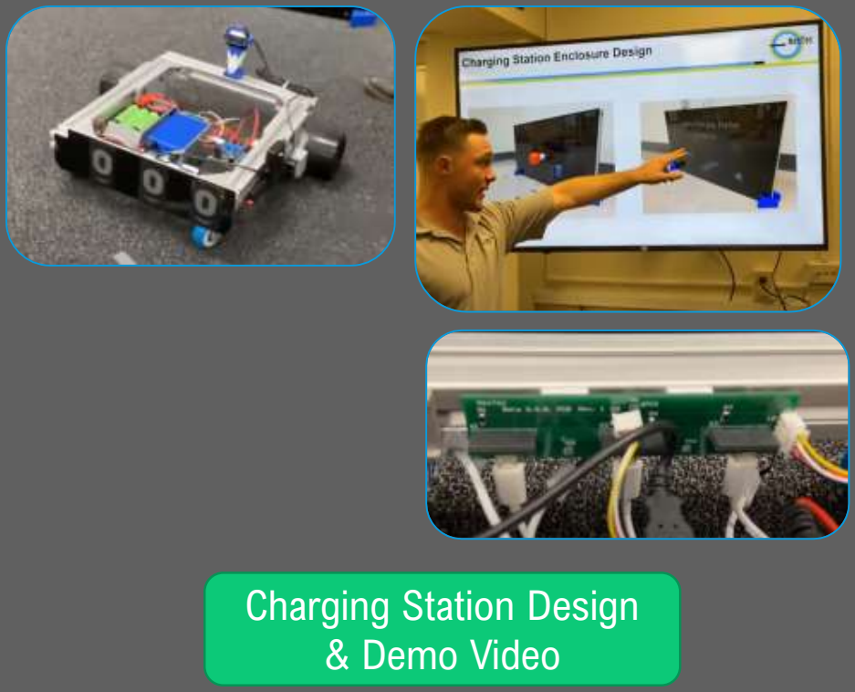
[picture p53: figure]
Charging Station Design & Demo Video

## Problem:

## - SCUTTLE has limited runtime unless

it can autonomously charge.

## Solution:

## - Utilize the charging system developed by NexTec Capstone team (2018) and enhance the software so that:

### - docking is fast and reliable - multiple robots can share the station - battery hardware is neat and easy to

use.

# PROJECT TOPICS: SOFTWARE BASED

## Projects that do not require additional actuators

### Applications Guide SECTION 2

# 2.1 ENVIRONMENTAL MAP MAKER

Task:
- Use only the onboard navigation sensors (LIDAR and SONAR)
- Create a map of a room using LIDAR. Implement a remote-control driving and send a command to switch to automatic mode for exploring the room.

Why it’s useful:
- many facilities (educational, industrial, personal) need upated maps
- robotic execution can discover changes from blueprints or furniture
- use SCUTTLE when there’s a gas leak or other dangerous conditions, instead of a person.

Why it’s feasible:
- You can use existing libraries for mapping and integration of low cost or high-fidelity LIDARs.

# 2.2 VISUAL TARGET DISCOVERY

Locate a visual target using machine vision. Collect data about the location of that object and report the data wirelessly.

# 2.3 RFID & SENSOR PAIRING

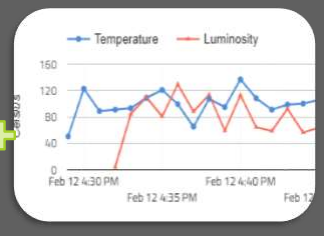
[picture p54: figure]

Scan multiple RFID tags and report environmental readings to the IOT for each location.

# 2.4 PAYLOAD IOT WEIGHING SYSTEM

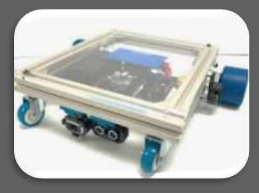
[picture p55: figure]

Locate the weight scale, measure the mass of the robot and exchange data with the scale as necessary to report the robot weight to the IOT

# 2.5 PARKING ENFORCEMENT

Parking enforcement such as “1-hour parking” is always a gamble because the checking routine is rarely standard.

It’s bad for guests who need to gamble if they have an extra 5 minutes and it’s bad for enforcers who struggle to keep fairness when they check spots

With no additional hardware, scuttle can be programmed to monitor important parking spots and indicate the status of all spots via web.

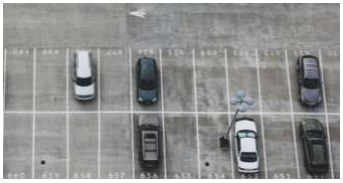
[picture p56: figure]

During Emergencies, SCUTTLE could even notify officials of empty spots when there is construction or obstructions in fire lanes, etc. This added value can offset the cost of adding robotics to small parking areas where scuttle must lap every 15 minutes or so.

# 2.6 3D IMAGE CAPTURE (3D SCAN)

Capturing 3D images of things outdoors is difficult and poorly executed with current solutions (namely, mobile apps). Several mobile apps render 3D models by circling a subject and taking photos at several angles.

The results of existing 3D capture systems are limited by the photographer’s ability to hold the camera:

- At a constant height
- Perfectly normal to the centerpoint of the object
- At the proper angular interval requested by the app.

SCUTTLE can use its precise wheel odometry and internal calculations to drive in a perfect circle around a subject. With a simple bracket, the camera can be mounted at an ideal height

Use: this technology could be used:

- by insurance companies to evaluate vehicle damage.
- Make 3D models of your self for a formal dress fitment.
- Request a quote to have a tree trimmed

# 2.7 PARKING GARAGE OCCUPANCY


Displace the hundreds of occupancy sensors in a large parking garage with SCUTTLEs. Program SCUTTLE to cruise past an array of parking sensors and communicate (over IoT) the status of all of the parking spots.

- How many spots are open?
- Where is the closest open spot?
- How long have spots been occupied?
- Is there an empty spot for extended periods? Maybe there is a shopping cart preventing cars from parking.

# 2.8 EVENT GUIDANCE

### Problem:

### - Everyday navigation is readily handled by mobile phones and google maps, but special events have custom destinations

and closed routes.

### Solution:

### - SCUTTLE guides people in festivals and events where temporary structures are in

place and google maps has no data.

### - County Fair

### - Major concerts

### - Olympic games

### - Oktoberfest, Carnaval

## Carnaval

Oktoberfest (https://shopmetaltech.com/machining-technology/cutting-tools/dispensing-with-tradition.html)

2.9 TACTILE FEEDBACK; Problem:; Robot drivers need to know if there is an obstacle that SCUTTLE encounters.; Solution:; Sense obstacles and inform the user via tactile feedback.; Use a lidar and a “safety bubble” radius, or a distance; Barrier; Gamepad

## sensor pointed down to detect

edges.

# PROJECT TOPICS: FEATURE BASED

## These projects add a feature, instead of a full behavior routine

### Applications Guide SECTION 3

# 3.1 COMPREHENSIVE TELEMETRY (SELF)


- Design a data structure to hold all major parameters of scuttles
- Design a data structure to carry these parameters for multiple scuttles in a fleet.
- Create a modular NodeRed dashboard with drag-and-drop functionality for new teams to gain awareness of their critical parameters while testing other tasks.

Submit your ideas to
scuttleProject@gmail.com | [Applications Guide] | © SCUTTLE Robotics LLC | 30

# 3.2 HOLOGRAPHIC DISPLAY


- Mount and integrate a hologram LED wand.
- Use the wand to display important metrics to users.

# 3.3 BATTERY CHARGING SYSTEM

- Option A: Wireless Charging
- Create a station which is child-safe by adding wireless charging to a dock where SCUTTLE navigates to receive a recharge.
- Option B: Battery changeout station
- Add more automation to the station itself and allow SCUTTLE’s battery to be removed and subsequently replaced.
- Design a modified battery pack which lends itself to quick recharge.

# 3.4 SOLAR CHARGING SYSTEM

- Operating as low as 7 watts, the SCUTTLE is a candidate for 100% solar sustainability.

10 Watt Solar Panel only $11.50 USD as of 2020 October

- Make SCUTTLE a long-term outdoor rover by designing a system to recharge the batteries by day and to “sleep” at night.
- If the solar module capacity is increased, it is possible to drive 24 hours per day while charging only for 10

# RECOMMENDED REFERENCES

## Great Places to Discover Ideas & Designs

### Applications Guide SECTION 4

# 4.1 YOUTUBE EDUCATORS


These exceptional youtubers
Frequently share free designs
Explain concepts and build simultaneously
Generate creative & inspiring projects

# 4.2 HARDWARE ENVIRONMENTS

Quick Release $16 [amazon]; Field Monitor Holder $25 [amazon]; 1KG Double Ball Swivel $9 [amazon]; Ball Head 360 $17 [amazon]; 4.2.1 Photography Hardware

Standard Photography hardware gives
interchangeability with
Moreover, we want to highlight hardware
that is Affordable, Available, and Off-the-
shelf in this section to enable users to
explore customizations.

SCUTTLE Models Library (https://www.scuttlerobot.org/category/models/)

# 4.2 HARDWARE ENVIRONMENTS

4.2.1 Continued:

Tripod adapter 4-pack AMAZON (https://www.amazon.com/Sametop-Adapter-Compatible-Session-Cameras/dp/B0126KXDN2)

Articulating Arm AMAZON (https://www.amazon.com/dp/B087T4T8D5)

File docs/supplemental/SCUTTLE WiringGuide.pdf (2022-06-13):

© SCUTTLE Robotics LLC –; 1 info@SCUTTLErobot.org; SCUTTLE Robot Wiring Guide; Revision 2022.06.13; Copyright 2022 SCUTTLE Robotics LLC

Arrow aligns with ground; space for probing; cover pins with hot glue; choose appropriate male pins

© 2022 SCUTTLE Robotics LLC – info@SCUTTLErobot.org | 2

# Good Practices

- Keep Wire sets bonded together.
- Use colors which are found in the common sequence
- makes it easy for others to repeat your trials
- makes it easy to document
- Eliminate individual pins
- replace them with multi-position housings
- Use black colored wire for ground
- whenever possible
- Dupont Housings: align the arrow to ground pin
- whenever possible
- Use 90-degree headers where appropriate
- Hot glue backs of through-hole pins
- reduce chance of short circuit
- hot glue is removable if necessary

# SCUTTLE Supports various CPUs

from the beaglebone schematic

© 2022 SCUTTLE Robotics LLC – info@SCUTTLErobot.org | 4

# Before You Begin:

Important Info:
To match the beaglebone pins to the pin numbers on the diagram:
The tiny white circle on the silkscreen at each connector indicates “pin1”

images of this style are copied directly

# Validated Sensors & Actuators

© 2022 SCUTTLE Robotics LLC – info@SCUTTLErobot.org; Dual Motor Driver; Pwr; Ultrasonic Sensor; Encoders; USB camera; Audio Amplifier; Gamepad Controller; Servos; Gamepad USB; Connection Map

# Motor Driver Signal Wires

Motor Driver Top View
HW-231 Motor Driver

JST-ZH 2-pin
1.5mm Pitch

Ground optional if

Blue has a common ground
to the battery pack.

Pin 1 should be HIGH when
motor is driven FORWARD

Hardware design convention:
Pin 1 uses the square solder pad.

Motor Direction:
Left-hand: Drives CCW on positive command.
Right-hand: Drives CW on positive command

# Motor Driver Power Wires

© 2022 SCUTTLE Robotics LLC – info@SCUTTLErobot.org; Right; Left; Input; To Power Supply; Power wires are 18 AWG

Motor Driver Top View
HW-231 Motor Driver

(Strip 6mm &
tin this end)

Solder & heat
shrink this end

Motor Direction:
Left-hand: Drives CCW on positive command.
Right-hand: Drives CW on positive command

# H-Bridge L298N (optional)

A versatile and cheap device for delivering variable voltage to low-powered DC actuators.

Connect any DC actuator

JST-ZH 2-pin
1.5mm Pitch

Ground pin not
required if
beaglebone shares
common ground to
input power.

Image adapted from
LastMinutEngineers.com (https://lastminuteengineers.com/l298n-dc-stepper-driver-arduino-tutorial/)

Pin 1 should be HIGH when
motor is driven FORWARD

More information about the 5v regulator
Found on the datasheet (L78M05) (https://www.generationrobots.com/media/ST_78M05DataSheet.pdf)

# Ultrasonic Distance Sensor (GPIO)

© SCUTTLE Robotics LLC – info@SCUTTLErobot.org; 3 2 1 0 3.3v GND; DuPont 4-pin; Vcc Trig Echo Gnd; 5.0v 3.3v GND GND; Beagle

JST-SH 4-pin

JST-SH 6-pin

NOTE: For JST connectors out-of-box,
the colors are not in the correct order.
You need to rearrange them.

# Beaglebone to I2C bus cable

(I2C port on Beagle)

2.54mm female 4-pin
(plugs into bus
board)

Plugs into I2C Bus PCB

# Compass CMPS or CMPS2 (I2C)

© SCUTTLE Robotics LLC –; 11 info@SCUTTLErobot.org; Compass; Gnd 3.3v SDA SCK 3.3v Gnd; Gnd 3.3v SDA SCK; I2C bus board

Compass Signal Cable

This compass is not necessary since you can
access the compass on the beaglebone blue. Be
sure to calibrate the compass on the blue since
it lies within close proximity of magnetic
hardware on the robot.

# Encoder Details

For the left-hand encoder,
A1 AND A2 solder is bridged.

The i2c address is determined by
the signals on A1 and A2 pins.

Left Hand Encoder A1 is pulled
down to GND. I2C address is 0x40

Pin A1 | Pin A2 | Resulting i2c address

Left Encoder | LOW | LOW | 0x40

Right Hand Encoder pin A1 is pulled
up to 3.3v. I2C address is 0x41

Right Encoder | LOW | HIGH | 0x41

## Option B: Order the custom PCB

GND; CLK; SDA; Screw Hole; Option A:; I2C Bus Board

DIY using perfboard / breadboard

The board is made from a breadboard and soldered
manually. The board can be cut between rows J & K.

You can order the custom PCB from JLCPCB.com or
any other service. We have posted the design files
on our github under electronics hardware. (https://github.com/scuttlerobot/SCUTTLE/tree/master/hardware)

The solder bridges all pins from left to right.

# Encoder AMS AS5048 (I2C)

Also see: Encoder Details Slide

Right Hand Encoder
A1 is pulled up to 3.3v
I2C address is 0x41
(Note mounting orientation on robot)

I2C bus board Left Hand Encoder
A1 is pulled down to GND
I2C address is 0x40

# Encoder Cables

Encoder ends (different); Right Hand; NC 3.3v NC SDA SCL A1 A2 GND; GND 3.3v SDA SCL 3.3v GND; Left Hand; NC 3.3v NC SDA SCL NC A2 GND

Cables modified as of 2020.12
SDA = GREY, SCL= WHITE

A1 & A2 soldered
together on PCB

Bus Board Ends
(matching)

20cm from tip to tip

# Battery

As an option, bridge
LiPo terminal to 12v
positive terminal (see
Servo Slide)

The "Battery Connector" is disconnected. Actual battery uses Barrel
Connector.

# Battery Pack (version1 configuration)

This battery pack was used
through 2020.09. The wires are
appropriate for the CAD
designs posted prior to version

You may build a battery pack
without a Battery Management
System (BMS) as shown here, or
copy our latest design which
includes BMS. See next slide.

Two pairs of Anderson
connectors are attached here.

Pack version 1
BMS: does not fit
Model on GrabCAD (https://grabcad.com/library/scuttle-battery-pack-v2-1)

Pack version 2
BMS: optional

# Battery Pack (v2, enhanced with BMS)

Switch PN:SRB22A2FBBNN 10A max current; Length (mm)

The BMS adds several functions to the battery pack.
Look out for a Youtube video covering the SCUTTLE
BMS soon (-DM 2020.11)

Anderson connectors, 35A contacts

Table of wires
to cut (11 total)

3-Cell 18650
Tray bottom side

Leave this hole clear
for a screw

Pack version 2 • BMS: optional • Model on GrabCAD • Access the model as a standalone assembly; Pack version 1 • BMS: does not fit • Model on GrabCAD • Access CAD model from within SCUTTLE assembly; Battery Pack Styles

© 2022 SCUTTLE Robotics LLC – info@SCUTTLErobot.org | 19

# LIDAR

Power Connector Diagram (lidar side)

If the indicated cable part
number is used for power to
the lidar, brown will be
crimped into the 12v positive
APP terminal and blue is
crimped into the negative.

Cable: 7000-12241-2150300 (https://www.automationdirect.com/adc/shopping/catalog/wiring_solutions/sensors_-z-_switches/micro_(m12)_normal_duty_q-z-d_cables/5-pole_micro_(m12)_cables/700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)
Cable-side connector (female pins)

LIDAR-side connector (male pins)

Typical Lidar power consumption: 2.1w

# GamePad

© SCUTTLE Robotics LLC –; 21 info@SCUTTLErobot.org; Button Behavior: • not pressed: 0 • Pressed: 1; axis 1+; axis 3+; axis 0+; axis 2+; select proper mode; Trigger: B6; Trigger: B7

Gamepad Controls Mapping

Axis behavior:
• Right returns positive values
• down returns positive values

• Outputs:
• Analog axes return values between -1
and 1
• These axes reach their limits before
the hard-stop.
• To discover the behavior graphically,
visit the html graphical test page here (https://gamepad-tester.com/)

Servos; positive terminal; solder to third pin; Without a power source available at the positive (third pin) input of the liPo connector, the board has insufficient current available to the servos to drive servos at full torque or to drive multiple servos.; Bridge Power to the liPo connector; Servo Channel 1; Servo Channel 8; A safe fix is to solder the positive terminal of the DC jack to the third pin of the connector shown. When a battery is connected, the pins correspond to 0.0v, 3.7v, and 7.2v terminals of a 2-cell lipo.; for positive, negative, and signal.

Read the silkscreen to see correct connector orientation

# RFID reader

Plug into 6-pin JST-SH
port on bbb.

# Audio Amp


RC522 low-cost
RFID Scanner

PAM8610 D Amp Board

Aux cord | usb adapter

To 12v power

22AWG or
larger wires

1-speaker is OK.

Pyle PCB3BK

To Beagle USB

Alternative:

The above setup will support at least 10 watts (this is actually quite loud – easy to hear in a crowded room).

It is also possible to find a speaker which receives BOTH power AND signal over USB. These will be more compact but less powerful. (The speaker shown is 3w max)

# GPIO Connections

3 2 1 0 3.3V GND; output /; Controls Red LED; output output 3.3V GND; iput output input output 3.3V GND; Default Config:

GPIO connectors:
JST-SH 6-pin

Example call for writing to this pin:
write(1,3,1) # arguments: port, pin, state

output / Controls Green LED

Example call for reading this pin:
read(0, 1) #arguments: port, pin

SCUTTLE naming convention
(used in L1_gpio.py)

Note: JST wires don’t come
with the proper color
sequence. They must be
rearranged.

Connector vector image
preserved for later use.

# GPIO Example - Relay

3v Relay with both Normally Open (NO) contact and Normally Closed (NC) contact.

GP0 connector
JST-SH 6-pin on
Beagle

Relays are appropriate for switching of high powered devices. For heavy pumps, motors, fans, or floodlights, it may be best to add a dedicated power source such as an ancilliary battery. Then, control the power to the device using logic-level signals and a relay or solid-state relay.

A great detailed writeup is here. (https://lastminuteengineers.com/two-channel-relay-module-arduino-tutorial/)

Heavy Duty
Pump

Heavy
Duty
Power
Supply

3
2
1
0
3.3V
GND

This kind of board usually includes an opto-coupler and your powered device does NOT need to share a ground with your microcomputer. There are two circuits here, isolated from each other.

© 2022 SCUTTLE Robotics LLC – info@SCUTTLErobot.org | 27

1
0
3.3V
GND

Successfully tested setup 2020.10.10
- Jumper pin is removed from Vcc pins
- Send GND and 5v to the device from Beaglebone PWR
- In our test, the 3.3v from Beagle was insufficient to drive the relays
- Our device was found to be active low although advertised as active high

in2
in1
Vcc
GND Image credit: Last Minute Engineers (visit) (https://lastminuteengineers.com/two-channel-relay-module-arduino-tutorial/)

# Twin Relays (tested)

5.0v

GND

The problem with active-low relays:
If you have an actuator which must not be actuated until the right moment, (such as a car horn we tested indoors) an active-low device may cause you trouble.

Unless the coil power is provided at the exact moment that the signal pin is driven high, there will be an actuation during startup. Consider this when you shop for a relay.

JST-SH 6-pin

JST-SH 4-pin

# Wifi Antenna

Users can replace the small onboard antenna
with their own selected antenna.

Antenna1 is used for WiFi

Antenna2 is used for Bluetooth

U.FL mini pci to SMA
pigtail

6dBi antenna offers
improved RSSI if
pointed properly.

# SCUTTLE Wire Routing


LIDAR USB:

LIDAR
POWER

12V
JUMPER

Beagle
Pwr

Motor
Pwr

Camera
USB

GamePad
USB dongle

USB
splitter

USB
splitter

RH
encoder

LH
encoder

i2c
cable
motor
signals

L PWR R

i2c
to bb

Left Encoder

Right Encoder BB
Blue

8-pin duPont
8-pin duPont

3-Cell Li-ion
Pack

SICK
Lidar

USB
(data)

i2C Bus Board


# Wiring Guide Section 2

## [Raspberry Pi] [Jetson Nano] [Edge AI]

# Pi Wiring Guide

## Contents:

This section covers single board
computers (SBCs) that conform to the
40-pin header design from Raspberry Pi

Note: Raspberry Pi was integrated after Beaglebone
Blue. For wiring elements corresponding purely to the
chassis, see Part 1.

# SCUTTLE Wiring Guide Pt2


© 2022 SCUTTLE Robotics LLC – info@SCUTTLErobot.org | 32
Pi version 3B shown | Pin Number Convention

# Pi - Motor Driver Signals

Top View; Left; Input; Right; Pins on Pi; GPIO17 GPIO27 GPIO22; GPIO18 GND GPIO23; 10cm cable

Keep the wires bonded
together, if possible.

HW-231 Motor Driver

See Motor Driver Power Wires
slide for these connections.

# Pi - Encoder AMS AS5048 (I2C)

See slide 7 for details

# Encoder Details

Left Encoder; Front View; Side View

For the left-hand encoder,
A1 AND A2 solder is bridged.

The i2c address is determined by
the signals on A1 and A2 pins.

Left Hand Encoder A1 is pulled
down to GND. I2C address is 0x40

Pin A1 | Pin A2 | Resulting i2c address

Left Encoder | LOW | LOW | 0x40

Right Hand Encoder pin A1 is pulled
up to 3.3v. I2C address is 0x41

Right Encoder | LOW | HIGH | 0x41

# Pi - Power Supply

Gnd DC-DC 15W Converter

# Dupont Cables

Motor Signals Cable

Ground: When possible, insert
the ground in the housing pin
with the arrow.

Opening: Make the opening face
the outside of the Pi headers
when plugged in. This makes it
easier to probe.

Bonding: Do not peel the wires
apart unless you must. Keep
wires bonded for strength

Pin Groups: Always use grouped
housings instead of individuals.
Then, the cable resists
tugging, unplugging, and bending
male pins.

Pi Power Wire

Tug Test: After inserting pins
into housings, lightly tug each
pin to ensure it is locked in.

# Voltage Meter – Adafruit INA219 This sensor can measure

© 2022 SCUTTLE Robotics LLC – info@SCUTTLErobot.org; Gnd 3.3v SDA SCK 3.3v Gnd; i2c bus board; INA219; To Battery Positive; To Load Positive; To Battery Negative; Load Negative

current and voltage.

Study an Example like this one (https://youtu.be/BgShCD7xT_A) if
you plan to measure current.

Set the i2c address to 0x44 by
bridging the A1 contact with solder.
See this guide (https://diyi0t.com/ina219-tutorial-for-arduino-and-esp/) for details.

The default Address of 0x40 would
interfere with the encoders.

© 2022 SCUTTLE Robotics LLC – info@SCUTTLErobot.org | 39
Distance Sensor – VL53L0X | This is a time-of-flight


© 2022 SCUTTLE Robotics LLC – info@SCUTTLErobot.org | 40

# Pi - Configuration for remo.tv

Coming for this slide: configuration of hardware on RasPi B 3+, Linux default device numbers for branded speakers, and text-to-speech selection (ie, alsamixer).

We recommend a speaker that receives power AND signals from the USB port.

If you need to use an Aux
cord, a right-angle adapter can keep your wires neat.


© SCUTTLE Robotics LLC – | 41 info@SCUTTLErobot.org

# Jetson Nano Wiring

40 Pin Array on Jetson Nano

Sysfs GPIO | Name | Pin | Pin | Name | Sysfs GPIO
| 3.3 VDC Power | 1 | 2 | 5.0 VDC Power
| I2C_2_SDA I2C Bus 1 | 3 | 4 | 5.0 VDC Power
| I2C_2_SCL I2C Bus 1 | 5 | 6 | GND
gpio216 | AUDIO_MCLK | 7 | 8 | UART_2_TX /dev/ttyTHS1
| GND | 9 | 10 | UART_2_RX /dev/ttyTHS1
gpio50 | UART_2_RTS | 11 | 12 | I2S_4_SCLK | gpio79
gpio14 | SPI_2_SCK | 13 | 14 | GND
gpio194 | LCD_TE | 15 | 16 | SPI_2_CS1 | gpio232
| 3.3 VDC Power | 17 | 18 | SPI_2_CS0 | gpio15
gpio16 | SPI_1_MOSI | 19 | 20 | GND
gpio17 | SPI_1_MISO | 21 | 22 | SPI_2_MISO | gpio13
gpio18 | SPI_1_SCK | 23 | 24 | SPI_1_CS0 | gpio19
| GND | 25 | 26 | SPI_1_CS1 | gpio20
| I2C_1_SDA I2C Bus 0 | 27 | 28 | I2C_1_SCL I2C Bus 0
gpio149 | CAM_AF_EN | 29 | 30 | GND
gpio200 | GPIO_PZ0 | 31 | 32 | LCD_BL_PWM | gpio168
gpio38 | GPIO_PE6 | 33 | 34 | GND
gpio76 | I2S_4_LRCK | 35 | 36 | UART_2_CTS | gpio51
gpio12 | SPI_2_MOSI | 37 | 38 | I2S_4_SDIN | gpio77
| GND | 39 | 40 | I2S_4_SDOUT | gpio78

Diagram from Jetsonhacks.com (https://www.jetsonhacks.com/nvidia-jetson-nano-j41-header-pinout/)

DC-DC ADAPTER

Plug into Nano power Jack
Nvidia recommends at least
2.5A, with 4.0A optimal for
peak power.

TDA4VM Edge AI Board; Edge AI Bracket; SCUTTLE i2c bus board; 40-Pin Header (matching Pi)

© 2022 SCUTTLE Robotics LLC – info@SCUTTLErobot.org | 43

# TDA4VM - Pinout

Power_3.3 | 1 | 2 | Power_5.0
I2C_SDA | 3 | 4 | Power
I2C_SCL | 5 | 6 | GND
GPIO | 7 | 8 | UART_TXD
GND | 9 | 10 | UART_RXD
GPIO | 11 | 12 | I2S_SCLK
GPIO | 13 | 14 | GND
GPIO | 15 | 16 | GPIO
Power_3.3 | 17 | 18 | GPIO
SPI_MOSI | 19 | 20 | GND
SPI_MISO | 21 | 22 | GPIO
SPI_SCLK | 23 | 24 | SPI_CS0
GND | 25 | 26 | SPI_CS1
ID_SDA | 27 | 28 | ID_SCL
GPIO | 29 | 30 | GND
GPIO | 31 | 32 | PWM0
PWM1 | 33 | 34 | GND
I2S_FS | 35 | 36 | GPIO
GPIO | 37 | 38 | I2S_DIN
GND | 39 | 40 | I2S_DOUT

Use USB-c to power the
TDA4VM SK board

# TDA4VM – SCUTTLE Wiring

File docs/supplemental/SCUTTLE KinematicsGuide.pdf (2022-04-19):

revised 2022.04.19

Copyright 2022 SCUTTLE Robotics LLC

©SCUTTLE Robotics LLC - Info@scuttlerobot.org

# SCUTTLE Kinematics

# This guide covers:

# - Robot geometry, r, and L

# - Key variables: phi, x, y, and theta - Kinematic equation: convert wheel speeds to chassis speeds - Inverse Kinematic equation: convert chassis speeds to wheel speeds - Time-derivatives of the wheel and chassis displacements - Rotation matrix to convert body-fixed coordinates to global coordinates

# SCUTTLE Coordinates

## xGLOBAL

NORTH

This slide is for reference.

The beagle circuit board has an IMU with y-axis pointing
along the USB port.

The global x- is often decided to be aligned with
magnetic North.

The SCUTTLE body-fixed X vector is aligned with the
forward direction.

# SCUTTLE: a Non-Holonomic System


A holonomic robot has the same number (or more) of controllable degrees of freedom as the number of degrees of freedom.

SCUTTLE DOF: (x, y, theta)
CONTROLLABLE DOF: (left motor, right motor) Mecanum Robot DOF: (x,y,theta)

In a non-holonomic system, the final position of the robot depends on the path taken to achieve the movement.

# Holonomic:

Easier navigation
More parts
Less robust

# Non-Holonomic:

Harder navigation
Fewer parts
More robust

Example:

Move right wheel, then left | Move left wheel, then Right

1
2

1
2

Suitable for
beginners

Requires knowledge
of kinematics


# SCUTTLE Kinematics

## - The Chassis Geometry determines the equations

for kinematics.

## - The radius, r, is the radius of the driven wheel - The half-wheelbase⁽¹⁾, L, is the space from wheel center to center divided in two


R = 41 mm | L = 201 mm (1)


# SCUTTLE Kinematics

# - Phi dot is the derivative of phi

with respect to time.

# ሶR = pdr, as in phi_dot_r

## ሶL = pdl, as in phi_dot_l

## phiDots = np.array( [ pdl, pdr ] ) # python syntax

# SCUTTLE Kinematics

## - Theta describes the difference between

global coordinate frame; cos(θ) −sin(θ); sin(θ); cos(θ); xbf; ybf

the body-fixed frame and the global
frame.

• The rotation matrix converts body-fixed
coordinates to the global coordinates


©SCUTTLE Robotics LLC
- Info@scuttlerobot.org

# SCUTTLE Kinematics

### - Phi is the angle of the wheel. – It is used to define incremental changes in wheel

### position and to calculate wheel speeds

- The x,y coordinate system has x pointing forward on the bot. – Positive movement of both phi’s result in positive

### movement of the robot along the x

### -direction

- The Kinematic Equation generates chassis motion information. – input the wheel speeds and output the (translational

### and rotational) chassis speeds

xሶ θሶ
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

# SCUTTLE Kinematics - Encoder

- Phi is the angle of the wheel.

### – Let ‘a’ be the encoder reading (from 0 to 360) – Let ‘N’ be the small:large pulley ratio

– Then,

- R = aR * N
- L = (360 - aL

) * N


# SCUTTLE Kinematics

## - Inverse Kinematic equation:

global coordinate frame; matrix multiplication:

– Input the desired speed and angular speed,
and output the left and right wheel speeds.
– These equations are written in the robot-
fixed frame
φሶL
φሶR

# SCUTTLE Kinematics

φሶL φሶR; Solve for

Forward and inverse kinematics in the robot frame:

“Kinematics”
Use the wheel speeds to
obtain the chassis speeds

“Inverse Kinematics”
Use the chassis speeds to
obtain the wheel speeds

# SCUTTLE Kinematics

Compute phi dots; left thumb input; I want to turn left; positive theta; dot; Desired phi dots; Generate θሶ value; Inverse kinematics

How do we use inverse kinematics?

Power motors:
achieve phi dots

global coordinate frame

# SCUTTLE Kinematics (prt 2)

## Describing the robot in the inertial (global) frame: - P0 describes the location of the robot and is defined by the

center of the wheelbase.

This section will be expanded to discuss navigation & inertial frame


Naming conventions for mobile platforms by ROS.org; What is a ROS node? Simple explanation; -ROS documentation; What is a twist message?

# Kinematics for ROS

ROS | SCUTTLE
speed.linear.x | x_dot or xd
speed.linear.y | always zero
speed.linear.z | always zero
speed.angular.x | always zero
speed.angular.y | always zero
speed.angular.z | theta_dot or td

“[Twist.msg] expresses velocity in free space broken into its linear and angular parts”

How to relate ROS twist
components with SCUTTLE?

What units are used for the twist message?; ROS; SCUTTLE; speed.linear.x; meters per; second; speed.angular.z; radians per; All recommended units by ROS.org

# Kinematics for ROS

- Twist.msg elements below are common (achievable) values to move SCUTTLE

Drive Straight; Point Turn CCW; Curve CCW; linear x; linear y; linear z; angular x; angular y; angular z

# Kinematics Footnotes

## 1) The true wheelbase is determined by

Inner edge: 355mm; Contact; Wheelbase; Ideal: 402mm

Wheel spec: 83mm diam

the contact patch of the wheels on
the ground.
• Most wheels have a draw angle from
the manufacturing mold, resulting in a
larger inner diameter.
• Then, the contact patch may lie closer
to the robot center, especially with no
payload.
• The inner wheel edge gives a 355mm
wheelbase.
• The wheelbase may change when a
heavy load compresses the urethane.

# Recommended reading:

1. Dhaouadi, Rached, and A. Abu Hatab. "Dynamic modelling of differential-drive mobile robots using lagrange and newton-euler methodologies: A unified framework." Advances in Robotics & Automation 2.2 (2013): 1-7.
2. Hur, Byul, et al. "Open-source Embedded Linux Mobile Robot Platform for Mechatronics Engineering and IoT
Education." Journal of Management & Engineering Integration 13.2 (2020): 34-44.
3. Achmad, MS Hendriyawan, et al. "ROS-based 2-D Mapping Using Non-holonomic Differential Mobile Robot." JURNAL INFOTEL 10.2 (2018): 75-82.

PDF (https://www.hilarispublisher.com/open-access/dynamic-modelling-of-differentialdrive-mobile-robots-using-lagrange-and-newtoneuler-methodologies-a-unified-frame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)

PDF (https://www.proquest.com/openview/c226e13db25063edb22c3e411af5dd0b/1?pq-origsite=gscholar&cbl=716332)

PDF (https://ejournal.st3telkom.ac.id/index.php/infotel/article/view/369/226)

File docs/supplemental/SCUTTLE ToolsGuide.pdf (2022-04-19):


© SCUTTLE Robotics LLC - info@SCUTTLErobot.org

# SCUTTLE Tools Guide

## PowerPole Crimpers


DuPont Crimpers | Spade Terminal Crimper

# Shared Tools (Recommended for Lab)

Throughout the design of the SCUTTLE robot, we co-selected tools and connectors to achieve a repeatable fabrication setup in a classroom environment. Achieve industrial quality without industrial tools.

## - Easy to use

## - Wide availability

## - Instructional videos online

Scissors | Wire strippers

## - Easy to use


# Flush Cutters

## - Wide availability

## - Instructional videos online

# Shared Tools (Recommended for Lab)

# Ferrule Crimper

Lab Recommendation:; in your lab.; shelves.

## - We recommend that you outfit your lab with 1 set of “shared tools” for every 4 robots

## - Also, 5S your labs by printing the previous slides out, laminating, and lining your

# Recommended Brands

## - We tested many brands of tools, including original

equipment manufacturer (OEM) and imitation brands.
We made comments here about value.
Tool | Brand on Amazon | Satisfied? | Comments
Anderson crimper | Zhushan (https://www.amazon.com/gp/product/B087473NBL/ref=ppx_yo_dt_b_search_asin_title?ie=UTF8&psc=1) | yes | Works like the original.
| Powerwerx (https://www.amazon.com/Powerwerx-TRIcrimp-Powerpole-crimping-Anderson/dp/B083PR6F2J?s=hi) (OEM) | Yes | This company is brilliant. Support OEM.
Electrician’s crimper | Gardner Bender (https://www.amazon.com/gp/product/B00079LN1Y/ref=ppx_yo_dt_b_search_asin_title?ie=UTF8&th=1) (OEM) | yes | Easy tolerances. It’s hard to mess this tool up.
DuPont Crimper | IWISS (https://www.amazon.com/gp/product/B017JU20Z6/ref=ppx_yo_dt_b_search_asin_title?ie=UTF8&psc=1) | yes | Never seen a crimper made by duPont but it’s probably expensive.
Soldering Iron | UY Chan TS100 (https://www.amazon.com/UY-CHAN-Programmable-Pocket-size-Acceleration/dp/B01MDTO6X7?s=hi) | Yes | Tested many awful irons in the past. The TS100 is by far our favorite. There seems to be no name brand, but the model is important. If it’s less than $60 it’s a fake.
Ferrule Crimper | Preciva (https://www.amazon.com/gp/product/B07XBLGPCY/ref=ppx_yo_dt_b_search_asin_title?ie=UTF8&psc=1) | yes | Many screwdrivers don’t live up to the name.
Flush Cutters | BOENFU (https://www.amazon.com/gp/product/B07KY8TYT3/ref=ppx_yo_dt_b_search_asin_title?ie=UTF8&th=1) | Mostly | Tons of brands out there. ONLY cut copper, solder, and soft alloys. Still, we never found a flush-cutter to last a long time. Tried Haako brand. Open to suggestions.
| Xytronic (OEM) | Mostly | Can’t even find this online, but it has a little more thickness to the cutting teeth, remains flush longer, but also cannot cut in tight spaces.
Wire Strippers | Neiko (https://www.amazon.com/gp/product/B000IYTCG6/ref=ppx_yo_dt_b_search_asin_title?ie=UTF8&psc=1) | Mostly | Nobody on our team agrees on the same “best” option so good luck.

# Tools for the Maker

- TS100 programmable soldering iron
- Safety Glasses (for all soldering work)
- Hot Glue Gun with temp control
- DC Power supply
- (capable of 10A output at 30v)
- Rosin flux pen
- Solder
- Leaded
- 0.8mm diameter

Recommended for all Roboticists!


# Tools for the Maker


- Powerwerx (or imitation brand) power meter
- Know if your MCU board has an issue
- Know how much your custom actuators pull during use
- Find out if your battery is charging or finished
- USB power meter


- Verify that your USB source is not limiting the power to your device (raspberry pi, cell phone, etc)
- Check the power consumption of added devices (usb camera, LED’s, WiFi dongle, etc.
- Electric Screwdriver
- We’ve bought multiple brands from Amazon and the highest ratings don’t have much impact for this product.
- The best value (currently) that we found is linked in the image.

Recommended for all Roboticists!


# Kits (suggested with each robot):

## - Allen Key

## - 6mm for M8 bolt

## - 4mm – for M6 screws


## - 2mm for M3 screws

## - SCUTTLE wrench (13mm hex wrench built in)

## - Phillips #1 hex-shank bit (for M2 course screws)


## These tools make teardown and rebuild of the SCUTTLE robot quick and easy. We recommend

that a lab is outfitted with 1 set for each robot.

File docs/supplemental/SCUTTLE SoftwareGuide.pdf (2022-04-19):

Last revised: 2022.04.19

Copyright 2022 SCUTTLE Robotics LLC

Comments? info@SCUTTLErobot.org

© 2022 SCUTTLE Robotics LLC - info@SCUTTLErobot.org

# Software Architecture

The SCUTTLE robot software has been programmed in Python3 on an embedded Linux platform. Both Beaglebone Blue and Raspberry Pi have been tested successfully. The software has been architected to make a robust starting point for students to create their own autonomous missions.

CONTENTS

LANGUAGE

FUTURE
OUTLOOK

This guide covers
- The parts of each software file
- How the programs interact with each other
- How the programs interact with hardware
- Sensor software vs actuator software

Next Steps: Robotic Operating System 2 (ROS2) is quickly becoming a reliable, versatile software platform for mobile robots. During 2022 the SCUTTLE team will release demos utilizing simultaneous localization and mapping (SLAM), aim to create a new ROS2 version of the software. Find a sneak peak of our python library intended for using in ROS, called scuttlepy. (https://github.com/ansarid/scuttlepy)

data

# Software Architecture – Introduction

The blocks in yellow are sensors, and the items in orange are actuators or other outputs. The level-2 blocks in teal are specific to the hardware platform (beagle, pi, etc) and perform communication with the low level devices. The blocks of level2 and above are non-hardware specific.

Each block aside from sensors and actuators represent an individual python program. The purple text indicates what important information is passed between programs and the black arrows indicate (for the most part) what direction the data is flowing. If a level 3 program needs information from another, it must receive the information from the top-level program, in order to maintain the structure of independence in program functions.

This software structure is preferred in order to perform subsystem testing. The data flowing through the top level is minimal and can be replaced with artificial data in the even that a sensor is unavailable.

Sensors

Actuators

programs

[var_A, var_B]

programs

# Software Architecture - Overview

Color Key; L2_kinematics.py; compute chassis movement; [pwmA, pwmB, pwmC,pwmD]; Motor Driver inputs 1,2; Motor Driver inputs 3,4; [duty_L, duty_R]; [phiL, phiR]; encoders; cpu clock; [x_dot,; theta_dot]; Left Encoder 0x40; Right encoder 0x41; Sensors; Level 2 Program (logic-defining); Level 1 Program (hardware-specific); Actuators; L3_drive_mt.py multithreading driving; GamePad controller; gamepad; [nearest obstacle]; [target_x_dot, target_theta_dot] +14 values; [target_phi_dot_L,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

L2_speed_control.py
generate wheel duty cycle
commands

L2_inverse_kinematics.p
y compute wheel vectors

[array of
distances &
angles]
L1_lidar.py
get the information from

L1_encoder.py

L1_gamepad.py

L1_motor.py
generate 4 signals to
output pins

L1_text2speech.py
generate audio signals for
aux output

Wheel Encoders Column

Game Controller Column

Motor Driver Column

Audio Output Column

# Software Architecture – Overview (continued)

[battery info] or
[temp, press] or
[mpu data]

L2_onboard.py
compute battery info

[mpu
values]
L1_mpu.py
get mpu data

[adc
L1_adc.py
get adc data

L1_bmp.py
get bmp data

L1_camera.py get the
image from camera

L1_servo.py
send commands to servos

Data logging column

# Libraries in use:

Python importing guidelines:

1. Each file should import the files below it in hierarchy, and not the files above it.
2. Each file may import non-scuttle libraries as needed (import NumPy, import time, etc.)
3. If the Level-1 file has imported an external library, it does not need to be imported by the Level-2 file

Libraries Utilized:

BeagleBone Blue Integration:

- RCPY (https://github.com/mcdeoliveira/rcpy) for communicating with MPU9250 & commanding motor drivers
- Adafruit GPIO (https://github.com/adafruit/Adafruit_Python_GPIO) for I2C Communication
- BMP280 (https://pypi.org/project/bmp280/) for communicating with the onboard bmp280 sensor.

Raspberry Pi integration:

- pysicktim (https://github.com/ansarid/pysicktim) for accessing LIDAR data
- gpiozero (https://gpiozero.readthedocs.io/en/stable/) for controlling GPIO pins.

Common Libraries

- os (https://docs.python.org/3/library/os.html) for making shell commands via python code.
- time (https://docs.python.org/3/library/time.html) for keeping track of time
- threading (https://docs.python.org/3/library/threading.html) for performing multithreading
- NumPy (https://www.numpy.org/) for performing math operations
- Fastlogging (https://pypi.org/project/fastlogging/) for generating log files
- pygame for accessing gamepad controller data
- cayenne.client (https://github.com/myDevicesIoT/Cayenne-MQTT-Python) for sending MQTT messages
- smbus2 (https://pypi.org/project/smbus2/) for accessing i2c bus through python commands

# Libraries Matrix

Lib | Beaglebone Blue | Raspberry Pi 3B+ and 4 | Jetson Nano [Under development]
Time | ✔ | ✔ | ✔
Threading | ✔ | ✔ | ✔
numpy | ✔ | ✔ | ✔
pygame | ✔ | ✔
fastlogging | ✔ | ✔ | ✔
Cayenne.client | ✔ | ✔
PySICKtim | | ✔
GPIOZERO | | ✔
RCPY | ✔
ADAFRUIT GPIO | ✔
BMP280 | ✔

Outline of an L1 Program; Explanation of the purpose; Import internal programs (if applicable); Import external programs (aka libraries). Take actions for initializations of objects or global variables.; Define functions. In some cases, make functions that combine other functions in sequence.; Offer a simplified, minimal loop for testing the code.; All files follow this outline when possible. The level-1 programs are most suited to this outline.

# Guidelines for Levels

Importing Files & Libraries; Sensor actual hardware; [raw data subset]; [raw sensor data]

pass data to L3

Testing
Code and Hardware

[data relevant
to the mission]

Only import L1 programs directly
below. Do not import L3 program. As
needed, import external libraries.

L2_program.py
compute parameters from L1 data

This file has a loop to test the whole
group (L1 + L2 + sensor).

Do not import L2 or L3 programs. As

L1_program.py
get the data from sensor

This file has a loop to test sensor
function.

When?

Do What?

# Multi-threading Purpose

- Threading offers better control over timing of code execution.
- Each thread should contain actions that are related and that should be executed within a specific time window.
- The user should avoid passing data between threads because it reduces robustness. Instead, call the level 2 program as needed in each thread, even if you need to communicate with the same device (ie, retrieve gamepad commands for driving and retrieve in parallel for speaking commands)
Thread 1 (driving) | Thread 2 (obstacle detect)

Drive the
robot

After
sampling
the
controller

AND

Log the
speed

After
sending
drive
command

Indicate
obstacles
using
speaker

when
obstacle is
detected by
lidar

Thread 3 (speaking)

20ms cylcle | 10ms cylcle

speak via
speaker

user presses
button

5ms cylcle

# Software Architecture: Sensors vs Actuators

Actuators; Actuator actual hardware; program; [message for actuator]; [message from; the mission]; [message for; L1 program]; Sensors; Sensor actual hardware; [raw data subset]; [raw sensor data]

pass data to L3

pass command from L3

Sensor and Actuators have the same architecture
except for data direction.

[data relevant
to the mission]

For sensors, the data is generated at the hardware
and sent UP.

L2_program.py
compute commands for L1

compute parameters from L1 data

For actuators, the data is generated at the top and
sent DOWN to hardware.

Some sensors and actuators have feedback and
preset commands, so data may flow both ways.

L1_program.py
get the data from sensor

send commands to actuator

# Software Architecture: Modularity & Robustness

myErrorLog.csv data log; Info retrieved for text2speech; functions: logSpeeds(); logError(); logNewDataType(); myLogMsg.txt data log; + new log.csv created data log; L1_log.py; compute parameters from L1 data; info for nodeRed charts

# Level 1: logging

Rather than interacting with hardware, the L1_log program interacts with other python files. It acts as a sensor in that it retrieves recorded data and it acts as an actuator in that it can receive data and perform an action with it (store it in a file).

L1_log.py program was initially designated as level2, but is being set as L1 going forward (2020.11)

Motor Driver Column; variables & their definitions: slope1 = input by user y_inflection = input by user x_inflection = slope1 / inflection_y slope2 = (1-inflection_y)/(1-inflection_x) x_trim = x – x_inflection y = inflection_y + x_trim*slope2; [duty]; compress(); [compressed; duty]

# Function Explained: Duty Compression

Duty compression, or motor signal scaling, helps reduce the dead band
where the wheels don’t turn. Sometimes, small commands of duty cycle give insufficient voltage to overcome friction.

Based on an earlier experiment, in forwards and backwards directions, duty cycles below 22% may result in some noise but no movement.

This deadband region can be difficult for a driver to handle and even more difficult for a control system. We could chop this section out entirely to solve the static condition, but in transient conditions we would exacerbate the nonlinearity that takes place crossing the deadband.

The Compression function “compresses” the deadband and spreads the range where the duty cycle maps to a nonzero wheelspeed.

To define the function, we basically just manipulate the initial slope, and the inflection point for the output, y.

# Multithreading example

L3_tellHeading.py
declare robot heading on

L2_speed_control.py
generate wheel duty cycle
commands

L2_inverse_kinematics.p
y compute wheel vectors

L1_encoder.py
get the information from

L1_gamepad.py

L1_motors.py
generate 4 signals to
output pins

compass driver in
RCPY Lib

L1_text2speech.py
generate audio signals for
aux output

Wheel Encoders Column

Game Controller Column

Motor Driver Column

Audio Output Column

# Color Tracking Example

Color Key; Camera Column; [image]; Sensors; Level 2 Program (logic-defining); Level 1 Program (hardware-specific); Actuators; L3_follow.py Object Following; L1_gamepad.py Not used; [target speeds]; Kinematics Column; cycles; [duty cycles]; [target_phi_dot_L,; target_phi_dot_R]; Wide-Angle Camera; [pwmA, pwmB, pwmC,pwmD]; Motor Driver inputs 1,2; Motor Driver inputs 3,4; [target offset from center]; [target offset

L2_speed_control.py
Converts speeds into duty

L2_track_target.py
Finds color target in range

L2_inverse_kinematics.py
Compute wheel vectors

L1_camera.py
Get image from USB
camera

L1_motor.py
Generate signals to
output pins

Motor Driver column

# Absolute Orientation

- SCUTTLE has a compass for orientation
- The compass is nothing but a 3-axis magnetometer
- Encoders can provide relative orientation
- Compass is required for global orientation
- The compass is embedded in the IMU (MPU-9250)
- It has 3 sensors oriented in the indicated directions
- L1_mpu.py accesses the magnetometer
- Each magnetometer requires calibration

global coordinate frame; Remember: Theta is defined as scuttle’s; this theta is positive

chassis x-vector minus the global x-vector

# Magnetometer Behavior

- An axis is at its MAXIMUM when it is aligned NORTH
- The axis is at its MINIMUM when it is opposing NORTH
- After calibration, we can achieve the behavior below

Values Desired by Direction Using X axis for example:; (magnetic north)
xscaled =; 2(x − xmin); (xmax − xmin); in a full circle.; Before Calibration; Min (microtesla); max (microtesla); AfterCalibration; Min (ratio to max); max (ratio to max)

### 2) Using the following equation, re-scale each axis

1) Discover the maximum and minimum values by rotating sensor

Permanent magnets influence the sensor, so calibration must be done on the robot, in position near the motors.

# Determining Absolute Orientation


- X and Y axes are sufficient information to give heading.
- Z axis returns zero if scuttle sits flat
- Theta is defined as rotation of SCUTTLE from the global coordinate frame, or y-prime
- positive theta means SCUTTLE is turned left from north
- We can define NORTH as the y-axis of the global coordinate frame

Theta is positive when scuttle points west Theta is negative when scuttle points east

Use arctan2(y, x) (https://docs.scipy.org/doc/numpy/reference/generated/numpy.arctan2.html) to return a heading

## arctan2 is the "element-wise arc tangent of y/x choosing the quadrant correctly."

## ATAN2(0.91, 0.42) returns 25 degrees

## Example:

y = 0.91 | x = 0.42 y-prime

y is pointed strongly north
X is pointed weakly north
both axes return positive values

# Speeds Tuning

(where L = wheelbase); Nominal conditions:; Wheelbase: 405mm

Vmax = 0.4m/s (measured by wheel speed)

These are general performance characteristics
you can expect when using the standard
SCUTTLE hardware:

max, motor pulley = 19.5 rad/s

max, wheel= 9.75 rad/s

Battery: 11.5 volts OC

With 1 wheel stopped and 1 wheel moving:

Motors: equipped with standard 200 rpm gearbox

Wheels: 83mm diameter urethane wheels

max, chassis= 1.98 rad/s (0.32 turns/sec)

Pulleys: motor = 15 teeth, wheel = 30 teeth

# Speeds Tuning

(where L = wheelbase); Nominal conditions:; Wheelbase: 405mm

Vmax = 0.4m/s (measured by wheel speed)

These are general performance characteristics
you can expect when using the standard
SCUTTLE hardware:

max, motor pulley = 19.5 rad/s

max, wheel= 9.75 rad/s

Battery: 11.5 volts OC

With 1 wheel stopped and 1 wheel moving:

Motors: equipped with standard 200 rpm gearbox

Wheels: 83mm diameter urethane wheels

max, chassis= 1.98 rad/s (0.32 turns/sec)

Pulleys: motor = 15 teeth, wheel = 30 teeth

# SCUTTLE Driving

- The left joystick operates the
robot wheels
- The forward/backward axis will request a speed
– (A.K.A movement in x)
- The left/right axis will request an angular velocity
– (A.K.A movement in theta)

requests xሶ


requests ሶ
Move | Theta_do t (rad/s) | X_dot (m/s) | Phi_d ot
max | 1.99 | 0.4 | 9.75

Given a measured max forward velocity of 0.4m/s, the other maximums are calculated.

axis 1+; axis 3+; axis 0+; axis 2+; select proper mode; Gamepad Controls Mapping; Trigger: B6; Trigger: B7

# SCUTTLE Movement Example

right turn on
joystick

Move | Theta_dot | X_dot | Duty_r | Duty_l

Fwd | 0 | 1 | 1 | 1
Rev | 0 | -1 | -1 | -1
right | -1 | 0 | -1 | 1
left | +1 | 0 | 1 | -1

POSTIVE differential on
NEGATIVE phi_dot_R

# SCUTTLE Movement Options

gamepad output; telepresence command; Kinematics function; Kinematics; function; (radians/sec)

To Generate an x_dot target

range of commands
(percent of max speed)

(meters/second)

ball tracking output

# SCUTTLE Color Tracking

1) SCUTTLE turns until the target is detected
within the threshold

2) After the target is in the center range, SCUTTLE drives
forward or backwards to reach a target radius, in pixels.

# Color Tracking: Radius

Target radius, r1 : 28; radius, tolerance: +/-3

To control x_dot motion, we evaluate the size of
the ball in the camera view.

If the ball radius is too large, we make a Reverse
command.

If the ball raidus is too small, we make a Forward

The requested angular speed for SCUTTLE is the x_offset (as a fraction of max) times the

In this case, the requested turning velocity is negative 0.5 * max speed (2 radians/second). This gives a 1 radian/second right hand turn.

3) The intensity of the turning request is computed, proportional to the offset of the detected object from

maximum range; Lidar Device

# LIDAR Concept of Operation

ANATOMY
Lidar systems have a rotating sensor collecting multiple measurements to measure in a 2D plane. (Some have 3D, by other methods).

METHOD
Lidar emits a beam of light and receives the reflection. distance is based on Time of Flight concept.

POWER
TiM561 uses about 2.1 watts during operation, mainly due to driving the motor and driving a strong IR emitter diode.

FAILURE MODES
Just like light, a Lidar beam can be absorbed by very dark objects and can be mis-directed by highly reflective objects which are non-perpendicular to the beam.

DATA QUALITY
The lidar has variable resolution in a sense! 0.33 degrees offers 5mm point spacing at a 1m distance, and at 10 meters, 50mm point spacing.

APPROPRIATE USE
To be successful in using the device, you need to see the datasheet (https://cdn.sick.com/media/docs/3/43/143/Operating_instructions_TiM55x_TiM56x_TiM57x_TiM58x_2D_LIDAR_SENSORS_en_IM0053143.PDF) to understand the parameters of your device.

# LIDAR – measuring a point

(degrees)]; LIDAR location; Center of Wheelbase

• The points will be initially measured from
lidar and returned as pairs given by:
• Python’s numpy library performs math in
radians. It is easy to convert back and forth
but you must be aware of your units.

is the location of the lidar.

# Software For LIDAR

Key Points:
Software is using the numPy library to handle vectors and matrices. numPy computation is faster than raw python and requires proper syntax.

Lidar scan frequency: 15hz, so you cannot get new measurements faster than 66ms.

L1_lidar.py returns 54 measurements by default and can return over 800 single points if desired, for more resolution.

TiM561 LIDAR returns distances in meters. Distances under 16mm are returned as error codes in case of poor reflection or other problem for a given measurement.

L2_vector.py can manipulate measurements, with functions such as returning the nearest point, combining cartesian vectors, and converting vectors from polar to Cartesian coordinates.

# Global Location of Obstacle

P2

Determine the global location of an obstacle:

You must add vector r0 and vector r02

First, your vector r02 must be generated using
knowledge of the location of the LIDAR on the
robot.

Where is the obstacle
located in the room?

vector r02
is not given
automatically.

# Global Location of Obstacle

Determine the global location of an obstacle:

Lidar is located at positive 254mm in the x-direction on the robot.

The lidar beam is 166 mm above the floor.

# Obstacle Avoidance by LIDAR


One method to avoid obstacles is to
generate an imaginary spring which
pushes on your robot and depends on
the nearest obstacle.

is the y-component of distance d

is the x-component of distance d

Obstacle Avoidance by LIDAR; Strategy:; • P2 LIDAR scan.; body-fixed frame; Cartesian coordinates

The obstacle avoidance feature will try to detect the nearest objects to the robot and apply an “invisible force” to prevent the robot from crashing. The force is intended to act like a spring which is anchored to the nearest obstacle and pushes the robot at a point on the body, referred to as P1.

The obstacle avoidance only deals with the body-fixed frame

- Define P1 as a point of interest on our robot.
is assigned to the nearest point detected by the
- d is the distance between point 1 and point 2
- We would like to handle all of these variables in:

# Obstacle Avoidance – influence on velocity (translational and angular)

• If P2 is detected straight ahead, the force influences velocity
• If P2 is detected at the side, the force influences steering
• If P2 is detected at an angle, the force will influence both

# Obstacle Avoidance – Variable Force

P2

large force; small force

• If d is large, the force is low
• If d is small, the force is high
• If d is larger than dmax, the force is absent

# Quick Dive – Barometric Pressure

COLLEGE STATION 4-DAY CHANGE
delta in pressure is 30.09-29.58 “Hg ➔ 0.51” Hg delta pressure = 1.73kPa

Historic weather at timeanddate.com (https://www.timeanddate.com/weather/usa/bryan-college-station/historic)

STANDARD PRESSURE CALCULATIONS sea level std pressure: 101.3kPa
pressure at 1000ft: 97.7kPa
delta pressure = 3.6kPa
elevation change represented by 1kPa = 278ft

## What the Barometric pressure will tell you: 1.73kPa change in pressure will represent

480ft altitude change.

# Speed Control

Nominal conditions:; •Measure position •Capture time •10hz is sufficient; •Just math; Update Phis; Update PhiDots; Chassis displacement; Chassis speeds

Update Shaft positions
(take reading)

Get Wheel Increments

This slide is dedicated to describing the wheel
speed measurements and calculation of
variables for speed control.

•Take derivatives
•Update latest wheelspeeds

•Integrate the wheel positions

Battery: 11.5 volts, open circuit

Motors: equipped with standard 200 rpm gearbox

Wheels: 83mm diameter urethane wheels

Pulleys: motor = 15 teeth, wheel = 30 teeth

•Compute the displacement in
theta and x

•Take derivative of last
movements w.r.t. change in
time since last sample.

# Driving FORWARD in Full Detail:

PWM | chA | chB | chA | chB

Where lies the difference
between left and right?
A: Where we plug in the

# Further Reading

- https://en.wikipedia.org/wiki/Holonomic_(robotics)
- Connector types
- http://dangerousprototypes.com/blog/2017/06/22/dirty-cables-whats-in-that-pile/ (http://dangerousprototypes.com/blog/2017/06/22/dirty-cables-whats-in-that-pile/)

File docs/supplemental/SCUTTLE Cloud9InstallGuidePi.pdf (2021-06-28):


# CLOUD9 INSTALLATION GUIDE

MICHAEL TOWNSEND | MECHINTELLIGENT LLC | info@scuttlerobot.org

# (Using Raspberry Pi)

SCUTTLE Robotics – v5.26

TABLE OF CONTENTS

INTRODUCTION

Cloud9 is the main software we use to operate the SCUTTLE. It is a cloud-based Integrated Development

Environment (IDE) that allows us to write, run, and debug applications from within a browser. The robust Cloud9

IDE also gives us the ability to easily view and manage our file hierarchy and run commands in the terminal.

This guide will give you comprehensive instructions for installing and configuring the Cloud9 IDE on your Raspberry

Pi. It is expected that you already have a Raspberry Pi flashed with the latest version of Raspbian OS Lite that you

can control using Secure Shell Protocol (SSH) and at least a basic understanding of Linux Command Line.

STEP 1: INSTALLING CLOUD9

In order to install Cloud9 you must have NodeJS installed on your Pi. NodeJS simply allows us to execute code

outside of a browser. We need that capability because we get the Cloud9 software by cloning it from an online

repository on GitHub. We will save that clone to a directory and then compile it to the Pi. Once Cloud9 has been

compiled successfully we will have access to it on our browser.

1. Begin by opening a terminal in Command Prompt or Git Bash, either will work, and login as the user Pi

using SSH. Then execute the following command in the terminal to install NodeJS and git:

sudo apt install -y git nodejs

2. Next, execute the following command to clone the latest version of Cloud9 to the directory ‘.c9sdk’:

git clone https://github.com/c9/core.git .c9sdk

3. Then to enter the new cloned directory, execute the following command:

cd .c9sdk

4. Execute the following command to run an installation script to compile the cloned directory to the Pi:

./scripts/install-sdk.sh

Please note that this installation can take quite some time to complete. It can vary depending on how good of a

connection the Pi has to the internet and the quality of the network it is on. Expect it to take at least 10-15 minutes

and possibly longer to finish.

5. When the compiling is finally completed you should see this in your terminal:

Figure 2

6. To get Cloud9 running, execute the command in yellow that is says to run in order to launch Cloud9:

node server.js -p 8080 -a :

7. Now open a browser and search for hostname.local:8080 where hostname is either the default

raspberrypi or whatever you may have changed it to such as scuttle601. Then the Cloud9 IDE should load.

a. If it loads successfully then congratulations, you have finished the installation of Cloud9 and are

ready to proceed to step 2, skip part b and c.

b. If Cloud9 does not load in the browser, go back to the terminal and execute the following

command:

node server.js -p 8080 -a : --listen 0.0.0.0

c. Now open your browser again and refresh the page to see if the Cloud9 IDE loads. If it loads

successfully then you are ready to proceed.

STEP 2: SET CLOUD9 TO START ON BOOT

Although we can access Cloud9 now, we are not done setting it up. If we left it as is, we would have to open a

terminal and manually start Cloud9 every time the Raspberry Pi booted up. What we want to do is enable Cloud9

to automatically start every time the Pi is booted up so that we can go directly to the browser, open Cloud9, and

begin working.

1. Go back to the Command Prompt or Git Bash terminal and type the following command, it will create a

Cloud9 service file:

sudo nano /lib/systemd/system/cloud9.service

2. The Cloud9 service file will then open in the terminal with a menu at the bottom, the file should be empty

since you just created it.

3. In the Cloud9 service file, type the following lines:

[Unit]

Description=Cloud9 IDE

After=multi-user.target network.target

[Service]

User=pi

WorkingDirectory=/home/pi/.c9sdk

ExecStart=/usr/bin/node /home/pi/.c9sdk/server.js -p 8080 -a : --listen 0.0.0.0 -w /home/pi

SyslogIdentifier=cloud9ide

[Install]

WantedBy=multi-user.target

4. Once you have that all typed, check it once again to make sure you typed it exactly as it is above. If it is all

correct then use ctrl-x to exit the file menu, then enter y when prompted to save the changes and finally

hit enter.

5. The modified Cloud9 service file will set up Cloud9 as a service and define the process it should follow

upon booting the Pi. To run the service file and reflect those changes, execute the following command:

sudo systemctl start cloud9.service

6. The above command should start Cloud9, verify that you are able to access it in your browser.
7. Then use the following command to verify that the connection is good and see if there are problems:

sudo systemctl status cloud9.service

8. If the status comes back as all good, then execute the following command to enable the service file to

cause Cloud9 to automatically run whenever the Pi is booted.

sudo systemctl enable cloud9.service

9. To test that everything works as it should, turn off the Pi and re boot it.
10. Then go to your browser and search for your hostname.local:8080. Cloud9 should then load successfully

without any additional steps.

Congratulations! You have correctly enabled Cloud9 to automatically run each time you re-boot the Pi. That

completes the setup part of this guide, but you still have a few steps to configure Cloud9 and verify that it works.

STEP 3: CONFIGURING CLOUD9

So now you have installed Cloud9 and set it up to automatically run when the Pi is booted up, but there are still

some things that need to be configured within the Cloud9 IDE before you start using it to control the SCUTTLE. The

main configurations we will do in this step involve changing the version of Python used to version 3 and installing a

few python modules.

1. Go to your browser and search for your hostname.local:8080 to open Cloud9.
2. First we need to modify which version of python is supported in Cloud9. To change this, go to the Cloud9

settings by clicking the gear in the top right of the IDE. This will open a preferences menu.

3. In the menu, navigate to Project Settings > Python Support > and change the Python version to Python 3.
4. Then close the preferences menu and navigate to the terminal at the bottom of the IDE.
5. The first python module we want to install is pip. To install pip, execute the following command:

sudo apt install python3-pip

6. The next python module to install is NumPy. To install NumPy, execute the following command:

sudo apt install python3-numpy

7. To work with the I2C board we also need to install the Adafruit GPIO. To do this, execute the command:

sudo pip3 install Adafruit_GPIO

Good job, you now have a properly installed, setup and configured version of the Cloud9 IDE on your Raspberry Pi.

The next and final step will have a couple of quick tests you can perform to test Cloud9 and verify that it functions

correctly.

STEP 4: VERIFY BY TESTING

In this step we will create a folder and a basic python script to verify that all the steps you have completed up to

this point were done correctly. After this step is done you will be ready to start operating your SCUTTLE using

Cloud9.

1. To do this, click on File in the top left of the IDE and select New File.
2. Use ‘ctrl+s’ to save the file and save it as ‘testing.py’ within the .c9sdk/ folder.
3. Then in the window for the testing.py file, type:

print(‘Hello World!’)

4. Again use ‘ctrl+s’ to save the changes to the file.
5. Now go to the bash terminal at the bottom of the IDE and type the following two commands:

cd ~/.c9sdk

python3 testing.py

6. This will navigate to the .c9sdk directory where the testing.py file is saved and then run the file. It should

print out ‘Hello World!’ in the terminal as you can see in Figure 3 below:


Figure 3

7. Then you can create a folder to store the testing.py file in.
8. Use the command mkdir followed by the name of the folder you are creating.

mkdir test

9. When you execute that command, you should notice a new folder appear on the left side of the IDE in the

file directory with the name you assigned it.

10. Then simply drag and drop the testing.py file into the new folder you created. Open the folder and verify

the file is in there. If that all runs properly then it ensures that Cloud9 works the way we set it up.

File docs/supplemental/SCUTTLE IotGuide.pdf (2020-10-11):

# SCUTTLE Robot

## SCUTTLE IoT Guide (version 2020.10.10)

This guide is not a requirement.

The purpose of this guide is to offer a central structure for the SCUTTLE fleet to communicate over IoT. Everything that follows is based on using MQTT as the IoT protocol.

## Inspiration:

For a couple of years, the department of Engineering Technology perused the web for easy IoT toolkits and discovered Cayenne which met the needs of wide-ranging student projects from transmission of data between [mobile phone + microcontroller + computers], which had a reconfigurable GUI with no required coding, and was free and easy to set up.

Since Cayenne offers services to many full scale corporate customers their topic structure was notable for the detail and thoroughness. The SCUTTLE MQTT Topic Hierarchy version 1.0 does not imitate the Cayenne structure but it carries several lessons learned from their system, all aimed at robustness.

## Benefits:

- In the classroom, instructors may use this guide to offer students a starting point for interacting with robotic data and for evaluation. Only once there is a template can the instructor see if students successfully produced data.
- For users with limited hardware, real-time IoT data will become available from SCUTTLE users globally for practice in performing data manipulation.
- For project designers starting with SCUTTLE chassis, there is a standard template to save time in deciding how to organize their data.
- For the SCUTTLE community to discover each other and help each other in new ways.

## Going forward:

We know that this structure will require changes in the future but it’s best to start something instead of waiting for the perfect. Plus, we already have a method to smooth future changes.

See a mistake? Please email scuttleProject@gmail.com

What is MQTT?; https://www.hivemq.com/blog/mqtt-essentials-part-1-introducing-mqtt/

MQTT is a protocol for machines to send messages to each other.

Please visit our favorite documentation to learn how MQTT works!

TRY OUT THE WEBSOCKET CLIENT

# Quick-Start Guide

Broker: Hive MQ; Host: broker.hivemq.com broker.mqttdashboard.com; Port: 8000 (from web) 1883 (from edge device); Example Topic: scuttle/fleet/onboard/444/temperature Example Payload: 24.5; Preferred Parameters

Client ID: your choice. May be auto-generated.

Other settings: usually leave as default.

# MQTT Topic Structure

fleet; onboard; ambient; xxx; pressure; temp; battery; humidity; voltage; gps; lat; lon; registry; tracing; owner; brand; wheel; diameter; location; country; infrastructure; type; yyy; function; mxet; partner; scuttle; data; cells; orientation; deg; payload

This list is not comprehensive. It
is designed to lay out a format
for your topic selections.

xxx = your robot number
yyy = your gadget number

# SCUTTLE ECOSYSTEM

Classroom robots Classroom robots Classroom robots Classroom robots; WEIGHT STATION; FIXED LIDAR; Capstone Team Robot; Classroom robots Classroom SCUTTLE 1; Fleet Research Bot1; Home; Project; RasPi; server; Project Developer’s Bot; Youtuber’s Bot; Katapult Workshop Bot1; Raffles High School SCUTTLE1; Malaysia; USA; JAPAN; INDIA; RUSSIA; Remo.tv Telepresence bot; Katapult Workshop Bot1 Katapult Workshop Bot1 Katapult Workshop Bot1 Katapult Workshop Bot1 Katapult Workshop Bot1; California

SHARING OUR DATA WILL
OPEN NEW POSSIBILITIES

# Example: Pub / Sub on mobile:


### Step 1: Connect

### Step 2: Subscribe

### Step 3: Publish

# Structure Explanation

## - Explanation is on the way…


## - This slide will explain why the proposed structure has been chosen and how to use

it effectively.

## - Most likely, it will need a video =)

# Best Practices

We don’t have a Networking Expert on our team but until then:

Frequency:
send out registry data once per hour or more. Then it will be very easy to notice if two people are sending data on the same channel

Robot Number:
Choose a 3 digit number for now. Also choose a 3 digit number for your accessories. If you mount your accessory on your robot, don’t treat it as a separate machine.

Broker:
Please use the same broker as us, so we can discover each other. If you use a different broker, nobody will find your data. If you think a different broker is better, please get in touch with us and maybe we will all switch!

Capitals/Lowercase:
Everything is in lowercase with no special characters. Just letters and numbers.

How things will Evolve:
MQTT is the Email of Things. Looking back at email evolution, tons of servers were offered but some surfaced over time as most popular (gmail, yahoo, etc). Common practices are not yet established. There are no rules. Our architecture is being implemented to DISCOVER problems and opportunities so we can be part of the evolution.

- How do I choose a device number?


- Just choose any device number you wish. But, before going forward, subscribe to a topic under that robot to see if any data is being published, indicating that number is taken.
- Country: We recommend you use the first 2 digits of your country code from https://countrycode.org/ then pick the last digit.
- What if my number gets taken?
- Email us with your ideas, or if you reach this problem. As of 2020, that is intended to be dealt with in a future outline.
- Is it secure?
- No but that’s OK. outgoing data is visible to the whole world. Incoming data will only include data you request.
- Can I make it secure?
- Yes. MQTT brokers offer client ID and passwords but you will need to research how to use them.
- What if I message on the wrong channel?
- That’s okay. Nothing bad will happen unless someone has created a dependency on having perfectly formatted data on every channel.
- What if someone spams my topic?
- That’s okay too. If it happens repeatedly, the community will notice and come up with a solution. As of 2020, mqtt bots aren’t creating spam on these channels.
- Why would I waste my time publishing information like my wheel diameter?
- The more you share with the community the more possibilities will open up. With new AI algorithms it will be possible to passively examine the whole robot fleet, detect nuances such as damaged batteries, or create benchmarks for performance that we can all use to

Q & A

SCUTTLE Robot See a mistake? Please email

Use cases are on the way; projects.; Use Cases; I want to; Use this Topic:; Subscribe to all SCUTTLE data; scuttle/#

## - This slide will explain how to choose a nice topic for a new kind of data, or for new

See all SCUTTLE data from robots | scuttle/fleet/#
Reserve scuttle number #212 for myself | scuttle/fleet/registry/location/212/country


# Using MQTT on Arduino?

Our favorite arduino Library: ArduinoMqttClient

Find it on github or add it through your Arduino IDE


# Troubleshooting – Error Codes

Find more info at VTSCADA.com

At times your device will alert you of an error in MQTT operation.

These codes are returned by the broker to the client when there is a problem with the connection or message. They can help in troubleshooting.

Error code (Decimal) | Error code (Hex) | Meaning
0 | 0x0 | No Error
1 | 0x1 | Connection Refused: Unacceptable protocol version
10 | 0xa | Timeout waiting for SUBACK
11 | 0xb | Timeout waiting for UNSUBACK
12 | 0xc | Timeout waiting for PINGRESP
13 | 0xd | Malformed Remaining Length
14 | 0xe | Problem with the underlying communication port

ERROR EXAMPLE

15 | 0xf | Address could not be parsed
16 | 0x10 | Malformed received MQTT packet
17 | 0x11 | Subscription failure
18 | 0x12 | Payload decoding failure
19 | 0x13 | Failed to compile a Decoder
2 | 0x2 | Connection Refused: Identifier rejected
20 | 0x14 | The received MQTT packet type is not supported on this client
3 | 0x3 | Connection Refused: Server Unavailable
4 | 0x4 | Connection Refused: Bad username or password
5 | 0x5 | Connection Refused: Authorization error
6 | 0x6 | Connection lost or bad
7 | 0x7 | Timeout waiting for Length bytes
8 | 0x8 | Timeout waiting for PayLoad
9 | 0x9 | Timeout waiting for CONNACK

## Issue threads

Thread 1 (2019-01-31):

update motor power diagram (Wiring Graphics Rev2019.01.30.pdf)

dmalawey, 2019-01-31:
this diagram shows ground and power labels reversed on the input phoenix connectors.  correct this on next version.

dmalawey, 2019-02-07:
New wiring diagram issued.

Closed 2019-02-07.

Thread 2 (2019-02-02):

Ultrasonic Page on Electronics Diagram shows incorrect GPIO Plug

ansarid, 2019-02-02:
The ultrasonic wiring diagram shows GP1 instead of the correct GP0.

Closed 2019-02-02.

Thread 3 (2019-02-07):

Easy I2C wiring test.

ansarid, 2019-02-07:
Shows position of both left and right encoders.

ansarid, 2019-02-18:
Currently only shows encoder values.
No compass.

Closed 2019-02-12.

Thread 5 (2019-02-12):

Create video on checking barrel plug voltage

dmalawey, 2019-02-12:
We need a video to show the functions of rc_test within SSH.

Please include instructions for the fewest commands to check the barrel plug voltage, for safety.

Let's mention it can be run also in cloud9

If we need to include a libary (adafruit BBIO?)  then we need to mention it's required, even if it was already installed in self_installer.sh

ansarid, 2019-02-12:
I can create a video showing both cloud9 and ssh. You should be able to measure from the adc out of the box.

Closed 2019-02-22.

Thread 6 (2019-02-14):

Get help with rc_test_servos issue

dmalawey, 2019-02-14:
Reach out for a solution to the problem of unable to drive multiple servos simultaneously.

dmalawey, 2019-03-07:
Issue resolved with 2s battery - details for solution are in the other issue concerning battery.

Closed 2019-03-07.

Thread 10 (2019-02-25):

Driving Servos over the Barrel Connector

ansarid, 2019-02-25:
I tried soldering the DC barrel power to the LiPo connector input which worked to still power the BeagleBone Blue when using only the DC barrel to supply power. When I connected some servos and ran `rc_test_servos -s 1.5` the BeagleBone shut off immediately after the command was run. I unpluged and then plugged the beaglebone back in the lights came back on but the beaglebone refused to boot. I tried the SD card in another BeagleBone and the SD still works fine.

Point is we need a different solution for powering the servos from the beaglebone using just the dc barrel plug.

dmalawey, 2019-03-07:
The required step for full functionality is to use a small 2S lipo that will be continuously recharged by our battery plugged into barrel jack.

JK, Feb 21, 2019 in youtube comment:
"@David Malawey The power is coming from the MP2615 charger IC. The regulator/motor load doesn't act like a battery and the MP2615 doesn't seem to be designed to provide a steady voltage without a battery load. Instead, it is going to oscillate between thinking the battery is full and in need of a charge. "

Closed 2019-03-07.

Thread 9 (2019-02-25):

Create PyGame replacement for matlab udp client.

ansarid, 2019-02-25:
Migrating all the tools to python for easier use across all devices.

ansarid, 2019-03-13:
Now using Tkinter instead of PyGame.

ansarid, 2019-03-28:
Seems unneeded at the moment. Postponing for later.

Closed 2019-03-28.

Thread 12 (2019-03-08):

Motor driving "signal handler error" or Segmentation Fault

dmalawey, 2019-03-08:
This output is given in concurrence with a disconnection of the beaglebone and a non-responsiveness to further commands.

/usr/local/lib/python3.5/dist-packages/rcpy-0.5.0-py3.5-linux-armv7l.egg/rcpy/__init__.py:127: UserWarning: > Installing signal handlers
  warnings.warn('> Installing signal handlers')

Message from syslogd@scuttle at Mar  1 22:46:44 ...
 kernel:[  649.327422] Internal error: : 1028 [#1] PREEMPT SMP ARM

Message from syslogd@scuttle at Mar  1 22:46:44 ...
 kernel:[  649.457984] Process python3 (pid: 1141, stack limit = 0xd1816218)

Message from syslogd@scuttle at Mar  1 22:46:44 ...
 kernel:[  649.464104] Stack: (0xd1817e18 to 0xd1818000)

Message from syslogd@scuttle at Mar  1 22:46:44 ...
 kernel:[  649.468482] 7e00:                                                       00000001 00000000

Message from syslogd@scuttle at Mar  1 22:46:44 ...
 kernel:[  649.476700] 7e20: 00000000 d1817e7c db49b500 c081df48 db49b520 00000000 00000000 dc7d9210

Message from syslogd@scuttle at Mar  1 22:46:44 ...
 kernel:[  649.484917] 7e40: d1817e74 d1817e50 c081b72c c081df54 c1504dc8 00000000 dc4e6f94 db49b500

Message from syslogd@scuttle at Mar  1 22:46:44 ...
 kernel:[  649.493134] 7e60: 00000002 dc5f3280 d1817eb4 d1817e78 c081be7c c081b618 00000000 00009c40

Message from syslogd@scuttle at Mar  1 22:46:44 ...
 kernel:[  649.501351] 7e80: 00000000 00000000 00000001 322c3fc2 00000002 c081be00 dc7d9200 00000000

Message from syslogd@scuttle at Mar  1 22:46:44 ...
 kernel:[  649.509568] 7ea0: 00000000 d1817f68 d1817ecc d1817eb8 c092f108 c081be0c c092f0e0 dc7d9200

Message from syslogd@scuttle at Mar  1 22:46:44 ...
 kernel:[  649.517786] 7ec0: d1817ee4 d1817ed0 c03855c4 c092f0ec 00000002 dc7d9200 d1817f1c d1817ee8

Message from syslogd@scuttle at Mar  1 22:46:44 ...
 kernel:[  649.526004] 7ee0: c0384c10 c0385580 00000000 00000000 db702988 c0384b18 dc4f3840 a6e18aec

Message from syslogd@scuttle at Mar  1 22:46:44 ...
 kernel:[  649.534222] 7f00: d1817f68 00000000 a6e18aec 00000002 d1817f34 d1817f20 c02f9258 c0384b24

Message from syslogd@scuttle at Mar  1 22:46:44 ...
 kernel:[  649.542439] 7f20: 00000002 dc4f3840 d1817f64 d1817f38 c02f943c c02f923c c031b088 c031bbd0

Message from syslogd@scuttle at Mar  1 22:46:44 ...
 kernel:[  649.550655] 7f40: c1504dc8 dc4f3843 00000000 00000000 dc4f3840 a6e18aec d1817fa4 d1817f68

Message from syslogd@scuttle at Mar  1 22:46:44 ...
 kernel:[  649.558872] 7f60: c02f96a4 c02f9394 00000000 00000000 00000002 322c3fc2 00000005 00000001

Message from syslogd@scuttle at Mar  1 22:46:44 ...
 kernel:[  649.567089] 7f80: 00000010 00000000 00000004 c01090e4 d1816000 00000000 00000000 d1817fa8

Message from syslogd@scuttle at Mar  1 22:46:44 ...
 kernel:[  649.575306] 7fa0: c0108f00 c02f9654 00000001 00000010 00000009 a6e18aec 00000002 a6e39620

Message from syslogd@scuttle at Mar  1 22:46:44 ...
 kernel:[  649.583522] 7fc0: 00000001 00000010 00000000 00000004 beccb290 0000000b 0000000c 0000000d

Message from syslogd@scuttle at Mar  1 22:46:44 ...
 kernel:[  649.591739] 7fe0: 00000000 beccb1d0 00000000 b6f303d0 000b0030 00000009 00000000 00000000

Message from syslogd@scuttle at Mar  1 22:46:44 ...
 kernel:[  649.670935] Code: e5980000 e6ffa07e eb049325 e5985028 (e1d570b0)

ansarid, 2019-03-12:
[rcpy Issue #14](https://github.com/mcdeoliveira/rcpy/issues/14#issue-371687150)

dmalawey, 2019-03-13:
I have documented this issue in the Beaglebone.org beagleboard - blue forum.   [Link is here](https://beagleboard.org/discuss?place=msg%2Fbeaglebone%2FcdywN2pd0_E%2FVkOEB_4MAgAJ)

dmalawey, 2019-03-13:
I have also pinged the RCPY author on his library's [existing issue](https://github.com/mcdeoliveira/rcpy/issues/14), with the same topic.

dmalawey, 2019-03-21:
I've now added this as an issue at [StrawsonDesign/LibRobotControl](https://github.com/StrawsonDesign/librobotcontrol/issues/154#issue-423478005) which I am told is the library truly handling this code, since RCPY is a python-written reference to librobotcontrol.

dmalawey, 2019-03-26:
The issue is being discussed in the slack channel for libRobotControl [here.](https://librobotcontrol.slack.com/messages/CBLL51BTL/)

User jadonk is creating some troubleshooting scripts associated with the errror [here](https://gist.github.com/jadonk/8ece4ad83ac67e5215af6a3d686d0ae2)

dmalawey, 2019-03-27:
A fix is in the works.  All users should update their librobotcontrol library, after running sudo apt-get update.

An example is shown below.  You can confirm that you have the latest librobotcontrol version by attempting to update it again, and receiving feedback that the library "is already the newest version"

```
debian@scuttle:~$ sudo apt-get update
[sudo] password for debian:
Ign:1 http://deb.debian.org/debian stretch InRelease
Get:2 http://deb.debian.org/debian stretch-updates InRelease [91.0 kB]
Get:3 http://repos.rcn-ee.com/debian stretch InRelease [3,061 B]
Get:4 http://deb.debian.org/debian-security stretch/updates InRelease [94.3 kB]
Hit:5 http://deb.debian.org/debian stretch Release
Get:6 http://repos.rcn-ee.com/debian stretch/main armhf Packages [912 kB]
Get:7 http://deb.debian.org/debian-security stretch/updates/main armhf Packages [466 kB]
Fetched 1,567 kB in 25s (61.2 kB/s)
Reading package lists... Done
debian@scuttle:~$ sudo apt-get install librobotcontrol
Reading package lists... Done
Building dependency tree
Reading state information... Done
The following packages will be upgraded:
  librobotcontrol
1 upgraded, 0 newly installed, 0 to remove and 0 not upgraded.
Need to get 399 kB of archives.
After this operation, 0 B of additional disk space will be used.
Get:1 http://repos.rcn-ee.com/debian stretch/main armhf librobotcontrol armhf 1.0.4-git20190227.0-0rcnee0~stretch+20190326 [399 kB]
Fetched 399 kB in 0s (828 kB/s)
Preconfiguring packages ...
(Reading database ... 53944 files and directories currently installed.)
Preparing to unpack .../librobotcontrol_1.0.4-git20190227.0-0rcnee0~stretch+20190326_armhf.deb ...
Removed /etc/systemd/system/multi-user.target.wants/rc_battery_monitor.service.
Removed /etc/systemd/system/multi-user.target.wants/robotcontrol.service.
Unpacking librobotcontrol (1.0.4-git20190227.0-0rcnee0~stretch+20190326) over (1.0.4-git20190107.0-0rcnee0~stretch+20190108) ...
librobotcontrol Package Uninstallation Complete
Setting up librobotcontrol (1.0.4-git20190227.0-0rcnee0~stretch+20190326) ...
Installing new version of config file /etc/modules-load.d/robotcontrol_modules.conf ...
Created symlink /etc/systemd/system/multi-user.target.wants/robotcontrol.service → /lib/systemd/system/robotcontrol.service.
Created symlink /etc/systemd/system/multi-user.target.wants/rc_battery_monitor.service → /lib/systemd/system/rc_battery_monitor.service.
leaving current robot control startup program alone
**********************************************
librobotcontrol package installation complete.
**********************************************
Processing triggers for libc-bin (2.24-11+deb9u4) ...
debian@scuttle:~$ sudo apt-get install librobotcontrol
Reading package lists... Done
Building dependency tree
Reading state information... Done
librobotcontrol is already the newest version (1.0.4-git20190227.0-0rcnee0~stretch+20190326).
0 upgraded, 0 newly installed, 0 to remove and 0 not upgraded.
debian@scuttle:~$

```

ansarid, 2019-03-28:
[The issue has been patched.](https://github.com/rcn-ee/librobotcontrol/commit/06c406de2c7b63a246a525f243d4e170ec0c664d)

Run:
```
sudo apt-get update
sudo apt-get install librobotcontrol
```

Closed 2019-03-28.

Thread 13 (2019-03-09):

Beaglebone does not connect via SSH anymore

TheGermanKid, 2019-03-09:
Not sure why but out of nowhere my beaglebone will not connect via ssh over usb. I checked my drivers but all are up to date and functioning. Wifi SSH still works when connected. I reflashed it but maybe someone else will run into this problem as well. I did change the wifi SSID and turned tethering on. Thats the only noticeable change I made but after that I was still ssh'ing via usb. Next day ssh via usb was not working.

Thanks

TheGermanKid, 2019-03-09:
Resolved: My computer was messing up, restarted it and it connects again.

Closed 2019-03-09.

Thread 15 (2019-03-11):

Build NEMA 17 gantry assembly

dmalawey, 2019-03-11:
[CAD models](https://grabcad.com/library/openbuilds-various-hardware-1) of similar design concept by OpenBuilds.

[Youtube video](https://www.youtube.com/watch?v=W2GxLMvkjQw) of mechanism operation style.

First few components in Solidworks CAD are uploaded on [grabCAD](https://grabcad.com/library/scuttle-linear-actuator-in-progress-1)

ansarid, 2019-03-30:
Issues driving servos and steppers at the same time.

ansarid, 2019-05-03:
Feature request by @jadonk on [](github.com/strawsondesign/librobotcontrol) for built in stepper control function.
[Issue #158](https://github.com/StrawsonDesign/librobotcontrol/issues/158#issue-429453060)

Closed 2019-09-17.

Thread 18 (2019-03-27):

Cannot SSH via wifi or USB to Beaglebone

SantiagoGarza96, 2019-03-27:
We were working with scuttle in Thom 101 and using the latest image scuttle_v1. When powered with the battery pack, the beaglebone network did not show up, and couldn't ssh via cloud9 or putty. While the beaglebone was powered via USB to a laptop and using putty to ssh to the address 192.168.7.2, a connection never occurred and would time out, same for cloud9.

ansarid, 2019-03-29:
User says issue fixed itself

Closed 2019-03-29.

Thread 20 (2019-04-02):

SICK lidar - Publish code to pull readings in Python

dmalawey, 2019-04-02:
1) Determine the communication method for the TiM561 over USB. \
e.g. if the communication is "serial" then what is the baud rate?\
Otherwise, determine the method, default IP address, port number, etc.\
2) share the spreadsheet that breaks down the "telegram" from the lidar.

dmalawey, 2019-04-02:
Attachments - example telegrams
[sample telegram.txt](https://github.com/MXET/SCUTTLE/files/3032186/sample.telegram.txt)
[telegram_translator_ver1.0.xlsx](https://github.com/MXET/SCUTTLE/files/3032187/telegram_translator_ver1.0.xlsx)

dmalawey, 2019-04-03:
from a SICK rep:

1) I found a surprisingly-detailed "how-to" in our internal support portal.  I attached the PDF and ZIP at the bottom that shows the process.  My research suggests that telnet programs can not readily connect to USB devices until a driver has "translated" the USB connection into some type of serial connection (COM1, COM2, etc).  The guide seems to show that the ROS driver can be used standalone (there's a link) but I'm not enough of an expert to say for sure.  Otherwise, there's a load of information in the PDF and ZIP to basically write your own driver...including example C code.
2) This guide looks extremely useful (and succinct!) to get the core ROS functionality loaded on a Beaglebone running the most recent Debian release (Debian 9 "Stretch")

[USB_interface.pdf](https://github.com/MXET/SCUTTLE/files/3041128/USB_interface.pdf)
[TIM_Linux.zip](https://github.com/MXET/SCUTTLE/files/3041129/TIM_Linux.zip)

dmalawey, 2019-04-04:
from an MXET senior:

here is a python program which will open and read from the USB port as a serial connection. It is commented fairly heavily with explanations of what is happening as well as links to documentation for several of the imports.

(after downloading, change the file extension to .txt)
[USBAsSerial.txt](https://github.com/MXET/SCUTTLE/files/3044561/USBAsSerial.txt)

ansarid, 2019-04-10:
Trying to build `TiM3xxLibUSBExample.c`
```
debian@scuttle:~/mxet_dev/LIDAR/TIM_Linux$ gcc TiM3xxLibUSBExample.c -o TiM3xxLibUSBExample
TiM3xxLibUSBExample.c:15:20: fatal error: libusb.h: No such file or directory
 #include <libusb.h>
                    ^
compilation terminated.
```
I tried installing libusb using apt-get and installed different versions of libusb which did not resolve the issue. I also built libusb from source which did not work.

ansarid, 2019-05-03:
I've now written [a simple library to use the TiM561 LIDAR over USB](github.com/ansarid/pytim5xx).

Closed 2019-05-03.

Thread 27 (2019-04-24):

Servo motor control problem

mortiz139, 2019-04-24:
Using two servos to control a robotic arm. I am currently trying to get one servo running, but as soon as I run the code nothing moves. My code is essentially based off what was provided in this github. I also tried running rc_test_servos too, and it still not move.

I keep on getting the "Installing signal handlers" warning. I have already done the two updates.
sudo apt-get update
sudo apt-get install librobotcontrol

My code is posted below

# import python libraries
import time, math
import getopt, sys

# import rcpy library
# This automatically initizalizes the robotics cape
import rcpy
import rcpy.servo as servo
import rcpy.clock as clock

# set state to rcpy.RUNNING
rcpy.set_state(rcpy.RUNNING)

# Create servo

clck = clock.Clock(baseservo, 0.02)

try:

	# enables all servos
	servo.enable()

	# start clock
	clck.start()

	# keep running
	while rcpy.get_state() != rcpy.EXITING:

		baseservo.set(1.3)

except KeyboardInterrupt:

	pass

finally:

	# stop clock
	clck.stop()

	# disable servos
	servo.disable()

	# say bye
	print("\nBye Beaglebone!")

ansarid, 2019-04-24:
The "Installing signal handlers" is just a warning, they can be ignored.

How are you powering your Beaglebone?

mortiz139, 2019-04-24:
I was using the power brick that was given to us to power it.

Sent from my iPhone

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

ansarid, 2019-04-24:
@mortiz139 Do you get any servo movement from running the command `sudo rc_test_servos -s 1.5`?

dmalawey, 2019-04-24:
@mortiz, next time you post code, use the "insert code" button so the formatting is understandable.

You can grab the servo example 1 from the python basics folder, and that will run 1 servo.  Then use the code below to expand that to two servos, plugged into channel 1 and 2.

If this works, take some time to review the difference between the basic example and the one here, so you can understand what's going on.

```
# This example moves two servos to the position specified by "duty," then reverses, then repeats.
# If the servo is a continuous type, the duty will set the speed instead of the position.
#To use this example, your servos must be connected to the first and second ports.

# import python libraries
import time, math
import getopt, sys

# import rcpy library
# This automatically initizalizes the robotics cape
import rcpy
import rcpy.servo as servo
import rcpy.clock as clock	# For PWM period for servos

# defaults
duty = 1.5	# Duty cycle (-1.5,1.5)
period = 0.02	# Set servo period to 20ms
channel = 1	# Which channel (1-8), 0 outputs to all channels
channel2 = 2

# set state to rcpy.RUNNING
rcpy.set_state(rcpy.RUNNING)

srvo = servo.Servo(channel)	# Create servo object
srvo2 = servo.Servo(channel2)

clck = clock.Clock(srvo, period)	# Set PWM period for servos
clck2 = clock.Clock(srvo2, period)

try:

	# enable servos
	servo.enable()		# Enables 6v rail

	# start clock
	clck.start()		# Starts PWM
	clck2.start()

	# keep running
	while rcpy.get_state() != rcpy.EXITING:

		srvo.set(duty)	# Set servo duty
		srvo2.set(duty)
		time.sleep(2)

		srvo.set(-duty)
		srvo2.set(-duty)
		time.sleep(2)

except KeyboardInterrupt:

	pass

finally:

	# stop clock
	clck.stop()

	# disable servos
	servo.disable()

	# say bye
	print("\nBye Beaglebone!")
```

mortiz139, 2019-04-24:
I am off campus grabbing lunch real quick, but I will try it once I’m back and let you know.

Sent from my iPhone

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

Closed 2019-04-24.

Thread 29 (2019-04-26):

ADC initialization error?

mortiz139, 2019-04-26:
I am currently just trying to run rc_test_servo. I am testing the code before I plug in a servo. Once I run the code below, this is the error I receive.

```
debian@scuttle:/var/lib/cloud9$ rc_test_servos -c 1 -p 0.0
ERROR in rc_adc_init, failed to open iio adc interface
Failed to write to 'state.settings'. EROFS: read-only file system, open '/var/lib/cloud9/.c9/state.settings' .
```

dmalawey, 2019-04-26:
This trial was repeated on a different beaglebone with the same SD card, and the code executes with no error, and servo runs properly.  Does this mean the blue has a problem?

ansarid, 2019-04-26:
@mortiz139 try running it with sudo

ansarid, 2019-05-03:
Inactive issue for what seems like a lack of knowledge instead of an issue. Closing.

Closed 2019-05-03.

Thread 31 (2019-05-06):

help! installing matplotlib

dmalawey, 2019-05-06:
I'm attempting to install matplotlib on my blue, but it failed.  Here's what happened:

```
debian@scuttle:/var/lib/cloud9$ pip install matplotlib
Collecting matplotlib
  Downloading https://files.pythonhosted.org/packages/1e/20/2032ad99f0dfe0f60970941af36e8d0942d3713f442bb3df37ac35d67358/matplotlib-2.2.4.tar.gz (37.0MB)
    99% |████████████████████████████████| 37.0MB 1.3MB/s eta 0:00:01Exception:
Traceback (most recent call last):
  File "/usr/lib/python2.7/dist-packages/pip/basecommand.py", line 215, in main
    status = self.run(options, args)
  File "/usr/lib/python2.7/dist-packages/pip/commands/install.py", line 353, in run
    wb.build(autobuilding=True)
  File "/usr/lib/python2.7/dist-packages/pip/wheel.py", line 749, in build
    self.requirement_set.prepare_files(self.finder)
  File "/usr/lib/python2.7/dist-packages/pip/req/req_set.py", line 380, in prepare_files
    ignore_dependencies=self.ignore_dependencies))
  File "/usr/lib/python2.7/dist-packages/pip/req/req_set.py", line 620, in _prepare_file
    session=self.session, hashes=hashes)
  File "/usr/lib/python2.7/dist-packages/pip/download.py", line 821, in unpack_url
    hashes=hashes
  File "/usr/lib/python2.7/dist-packages/pip/download.py", line 659, in unpack_http_url
    hashes)
  File "/usr/lib/python2.7/dist-packages/pip/download.py", line 882, in _download_http_url
    _download_url(resp, link, content_file, hashes)
  File "/usr/lib/python2.7/dist-packages/pip/download.py", line 603, in _download_url
    hashes.check_against_chunks(downloaded_chunks)
  File "/usr/lib/python2.7/dist-packages/pip/utils/hashes.py", line 46, in check_against_chunks
    for chunk in chunks:
  File "/usr/lib/python2.7/dist-packages/pip/download.py", line 571, in written_chunks
    for chunk in chunks:
  File "/usr/lib/python2.7/dist-packages/pip/utils/ui.py", line 139, in iter
    for x in it:
  File "/usr/lib/python2.7/dist-packages/pip/download.py", line 560, in resp_read
    decode_content=False):
  File "/usr/share/python-wheels/urllib3-1.19.1-py2.py3-none-any.whl/urllib3/response.py", line 432, in stream
    data = self.read(amt=amt, decode_content=decode_content)
  File "/usr/share/python-wheels/urllib3-1.19.1-py2.py3-none-any.whl/urllib3/response.py", line 380, in read
    data = self._fp.read(amt)
  File "/usr/share/python-wheels/CacheControl-0.11.7-py2.py3-none-any.whl/cachecontrol/filewrapper.py", line 63, in read
    self._close()
  File "/usr/share/python-wheels/CacheControl-0.11.7-py2.py3-none-any.whl/cachecontrol/filewrapper.py", line 50, in _close
    self.__callback(self.__buf.getvalue())
  File "/usr/share/python-wheels/CacheControl-0.11.7-py2.py3-none-any.whl/cachecontrol/controller.py", line 275, in cache_response
    self.serializer.dumps(request, response, body=body),
  File "/usr/share/python-wheels/CacheControl-0.11.7-py2.py3-none-any.whl/cachecontrol/serialize.py", line 86, in dumps
    data, separators=(",", ":"), sort_keys=True,
  File "/usr/lib/python2.7/json/__init__.py", line 251, in dumps
    sort_keys=sort_keys, **kw).encode(obj)
  File "/usr/lib/python2.7/json/encoder.py", line 210, in encode
    return ''.join(chunks)
MemoryError
debian@scuttle:/var/lib/cloud9$
```

ansarid, 2019-06-09:
Matplotlib isn't useful to be installed on the BeagleBone. But this looks like your SD card does not have enough space.

Closed 2019-06-09.

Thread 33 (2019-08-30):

Self_installer.sh does not complete

dmalawey, 2019-08-30:
The self_intaller does not finish it's job of installing packages and many errors follow.

An example of the output is shown in this gist:  [problems with self_installer](https://gist.github.com/dmalawey/548086df8b3069f73360ee25d0f626f2)

dmalawey, 2019-08-31:
A resolution to this problem has been generated (with help from Ahmad B.)  We will reopen the issue if this fix is not successful for other users.

**Please note the fix:**
The self-installer starts by expanding the partition containing the image on the SD card, so there is room for additional installations of packages.  After this "growing" of the partition we need to reboot so the machine recognizes the larger partition space.

*The new self_installer has been modified to have two parts.  After the first part, a reboot is commanded. *

**Steps for the new process:**

- Reflash the SD card
- Reconnect to wifi using the tamulink_wpa process or using [this process](https://gist.github.com/dmalawey/e4be9f3b5beba8ed49868065935127b7) at home.
- Run the self_installer [part 1](https://github.com/MXET/SCUTTLE/blob/master/software/scripts/self_installer_part1.sh)
- After the machine reboots, reopen a terminal and run self_installer [part 2](https://github.com/MXET/SCUTTLE/blob/master/software/scripts/self_installer_part2.sh)

ReinhardtTanner, 2019-09-02:
I was able to complete self installer part 1, however I keep losing connection in cloud9 during step 2.

This is being done on my network at home because TAMU won't even let me do self installer part 1 for some reason.
I'm getting a read only error on the TAMU network.

An image is attached displaying the error.
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

dmalawey, 2019-09-02:
@ReinhardtTanner, you flashed using the very top version on the beagleboard.org/latest webpage, correct?  The name is **Debian 9.5 2018-10-07 4GB SD IoT**

The version called "flasher" may cause a problem since it attempts to write to the Blue's memory directly and subsequently will boot from onboard memory, limited to 4gb.

ReinhardtTanner, 2019-09-02:
Let me redo the process so I can narrow down a single issue.

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
--

*Michael T. Reinhardt*
Junior in Multidisciplinary Engineering Technology - Mechatronics

ReinhardtTanner, 2019-09-02:
Just checked, looks like I used the version below it, the LXQT version. I
am currently downloading the correct file (IoT) and then I will re-flash.

On Mon, Sep 2, 2019 at 10:36 AM Michael Reinhardt <reinhardttanner@tamu.edu>
wrote:

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

--

*Michael T. Reinhardt*
Junior in Multidisciplinary Engineering Technology - Mechatronics

ReinhardtTanner, 2019-09-02:
Hey David I reflashed the correct version from the BeagleBoard site, however I am still having the read only issue. I am currently on my home network. Below is the terminal text.

debian@beaglebone:/var/lib/cloud9$
debian@beaglebone:/var/lib/cloud9$ cd ~
debian@beaglebone:~$ sudo bash self_installer_part1.sh
sudo: unable to open /var/lib/sudo/ts/debian: Read-only file system
[sudo] password for debian:
debian@beaglebone:~$

dmalawey, 2019-09-04:
I think the next step is to learn what's going on with the space on the drive.  Please run commands from this video and output info on your boot drive.

https://youtu.be/SzzNJBzTZss

@ansarid  please add other useful troubleshooting questions to check on.

ansarid, 2019-09-04:
@ReinhardtTanner At exactly which step in the lab does this issue arise or become apparent?

ReinhardtTanner, 2019-09-18:
Ok so the issue was resolved. It seemed like it was a problem with the board as the WiFi and connection to the Beagle from computer frequently dropped upon attempted execution of the install files. The two install files installed flawlessly once a new board was obtained. Keep in mind the SD card remained unchanged with the previous flash version.

Closed 2019-09-25.

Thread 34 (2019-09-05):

Internet connectivity issue for BeagleBone. Input/output error

jessaggie, 2019-09-05:
Any attempted at connecting to the internet results in an input/output error. This includes trying to use
```
ping google.com
```
 as well as the
```
connmanctl
```
```
debian@scuttle:~/basics$ connmanctl -h                                             
bash: /usr/bin/connmanctl: Input/output error
```

ansarid, 2019-09-05:
@jessaggie Do all commands return the `Input/output error`, or just some commands?

jessaggie, 2019-09-06:
All commands returned the input/output error.

On Thu, Sep 5, 2019 at 11:05 AM Daniyal Ansari <notifications@github.com>
wrote:

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

jessaggie, 2019-09-11:
We have resolved this issue, possibly by reflashing the board

Closed 2019-09-11.

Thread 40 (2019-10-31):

import cv2 error

destantraeger, 2019-10-31:
Both self_installer_part1.sh and self_installer_part2.sh were run and cv2 was not installed in the user library. This issue persists across multiple teams.

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

ansarid, 2019-11-04:
@destantraeger If this issue has been resolved please let me know that it has been resolved and what the issue is so that I can close this issue. If I do not get a response within the next day I will consider this issue resolved and the issue can be reopened if that is not the case.

Closed 2019-11-04.

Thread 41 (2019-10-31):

Cannot get cv to work

TWR2020, 2019-10-31:
when we tried to run:
sudo bash start_mjgp_streamer.sh L3_image_filter.py
we are receiving this error.

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

ansarid, 2019-10-31:
@TWR2020 Please copy and paste the output. Do not attach screenshots of your issue.

ansarid, 2019-11-04:
@TWR2020 If this issue has been resolved please let me know that it has been resolved and what the issue is so that I can close this issue. If I do not get a response within the next day I will consider this issue resolved and the issue can be reopened if that is not the case.

TWR2020, 2019-11-05:
we are still having the same issue here is a copy of the output also.

debian@scuttle:~/basics/computer_vision$ ls
L3_image_filter.py  start_mjpg_streamer.sh
debian@scuttle:~/basics/computer_vision$ sudo bash start_mjpg_streamer.sh L3_image_filter.py
[sudo] password for debian:
MJPG Streamer Version.: 2.0
ERROR: could not find input plugin
       Perhaps you want to adjust the search path with:
       # export LD_LIBRARY_PATH=/path/to/plugin/folder
       dlopen: /usr/lib/mjpg-streamer/input_opencv.so: cannot open shared object file: No such file or directory
debian@scuttle:~/basics/computer_vision$

TWR2020, 2019-11-05:
we have run both of the self installers also here is the code again.

`debian@scuttle:~/basics/computer_vision$ ls
L3_image_filter.py  start_mjpg_streamer.sh
debian@scuttle:~/basics/computer_vision$ sudo bash start_mjpg_streamer.sh L3_image_filter.py
[sudo] password for debian:
MJPG Streamer Version.: 2.0
ERROR: could not find input plugin
       Perhaps you want to adjust the search path with:
       # export LD_LIBRARY_PATH=/path/to/plugin/folder
       dlopen: /usr/lib/mjpg-streamer/input_opencv.so: cannot open shared object file: No such file or directory
debian@scuttle:~/basics/computer_vision$`

ansarid, 2019-11-05:
@TWR2020 Please run `check_installed.sh` located in the scripts folder  and then try running `bash start_mjpg_streamer.sh L3_image_filter.py` again. Please send me the output of both commands.

ansarid, 2019-11-05:
@TWR2020 Please run `check_installed.sh` located in the scripts folder  and then try running `bash start_mjpg_streamer.sh L3_image_filter.py` again. Please send me the output of both commands.

TWR2020, 2019-11-05:
I ran the check_installed.sh and it installed a line for opencv however after doing this I ran the next command and I now cannot find the output as the terminal history is not long enough.
When I ran the `bash start_mjpg_streamer.sh L3_image_filter.py` it created a output that had statements about errors in it. When I ran the bordered flow I only saw one video stream image.

`FileNotFoundError: [Errno 2] No such file or directory: '/tmp/h_min'
Traceback (most recent call last):
  File "./L3_image_filter.py", line 25, in colorTracking
    with open('/tmp/h_min') as h_min_file:`

TWR2020, 2019-11-05:
This is an image of the nodered dashboard
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

dmalawey, 2019-11-05:
This image is working properly.  Move the sliders to adjust your mask.

dmalawey, 2019-11-05:
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

@ansarid could we update it to not look for the values until the sliders have been moved once?  Maybe pre-assign some values in the .txt files.

TWR2020, 2019-11-05:
I just figured that out reran it and adjusted the values and everything seems so be working properly.
thank you.

ansarid, 2019-11-06:
Sounds like this issue has been solved.

Closed 2019-11-06.

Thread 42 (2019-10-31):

USB Audio Issue

RMC-800, 2019-10-31:
# I lose connection from the gamepad and the speaker stops working when I run L3_drive_mt.py with both the USB dongle and a USB audio input device connected to the USB hub.

# These are the steps to reproduce this error.

#1). Connect the gamepad dongle and the USB audio to the USB hub and make sure the hub is connected to the BeagleBone.
#2). Run L3_drive_mt.py and check the functionality of the wheel control by moving the joystick. This should work fine.
#3). Press a button, such as button (X), to make SCUTTLE talk. May hear SCUTTLE say something once, but will cause gamepad to stop controlling wheels or send any more commands for speaking.
#4). Will have to open up a new terminal to cancel as this prevents me from stopping the program via ctrl^C.
#5). No error outputs are produced.

dmalawey, 2019-11-03:
If you want to use DriveMT, please confirm you have latest versions of all dependent files.  (almost every python file in basics folder).   The drivers for bmp have to be working as well.  As you can see if you review the speaking loop, this loop accesses some sensors now to produce feedback.  Probably there's an issue with the speaking loop on your bot.

I'm planning to take down the DriveMT file since it uses hardware not included on all robots.  It will be replaced eventually by a simple multithreading example.

Closed 2020-01-31.

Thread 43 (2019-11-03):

name 'lidar' is not defined

jessaggie, 2019-11-03:
Lidar is not defined even when it is defined.
We have verified the system recognizes it.
We are using the TiM781 lidar.
After playing around we believe it is a read/write issue but could be wrong.

Running the L1_lidar file gave us this error. It is in the same location as the pysicktim file.
The vendor id and product id are also exactly the same.

`debian@scuttle:~/basics/pysicktim$ python3 L1_lidar.py
Traceback (most recent call last):
  File "L1_lidar.py", line 48, in <module>
    lidarData = polarScan(54)
  File "L1_lidar.py", line 19, in polarScan
    lidar.scan() #take reading
  File "/home/debian/basics/pysicktim/pysicktim/pysicktim.py", line 351, in scan
    send('sRN LMDscandata')
  File "/home/debian/basics/pysicktim/pysicktim/pysicktim.py", line 196, in send
    lidar.write(2|usb.ENDPOINT_OUT,"\x02"+cmd+"\x03\0",0)
NameError: name 'lidar' is not defined`

ansarid, 2019-11-03:
@jessaggie It looks like the library was not installed correctly. Please read the instructions on the pysicktim README.md. Also please post any issues regarding the pysicktim LiDAR on the pysicktim repository issues tab.

dmalawey, 2019-11-03:
@jessaggie are you using the L1_lidar.py file that I updated yesterday?   Please confirm you have the latest.

jessaggie, 2019-11-03:
We were using the latest L1_lidar.py file.  Ran installation again and it worked this time. Thanks!

Closed 2019-11-03.

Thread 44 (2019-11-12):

RFID Reader Help

TWR2020, 2019-11-12:
We are trying to use the RFID reader and are not sure what we are doing wrong. We wired the device as shown in the diagram and followed the code setup from the L1_rfid.py file. We then tried to write and read a tag however it does not appear to work and wanted to ask for advice. Below are samples of the code we ran.Thank you

**Sample of the Setup code**
`debian@scuttle:~$ git clone https://github.com/ansarid/MFRC522-python
fatal: destination path 'MFRC522-python' already exists and is not an empty directory.
debian@scuttle:~$ cd MFRC522-python
debian@scuttle:~/MFRC522-python$ sudo python3 setup.py install
/usr/lib/python3.5/distutils/dist.py:261: UserWarning: Unknown distribution option: 'long_description_content_type'
  warnings.warn(msg)
running install
running bdist_egg
running egg_info
writing dependency_links to mfrc522.egg-info/dependency_links.txt
writing mfrc522.egg-info/PKG-INFO
writing requirements to mfrc522.egg-info/requires.txt
writing top-level names to mfrc522.egg-info/top_level.txt
reading manifest file 'mfrc522.egg-info/SOURCES.txt'
writing manifest file 'mfrc522.egg-info/SOURCES.txt'
installing library code to build/bdist.linux-armv7l/egg
running install_lib
running build_py
creating build/bdist.linux-armv7l/egg
creating build/bdist.linux-armv7l/egg/mfrc522
copying build/lib/mfrc522/MFRC522.py -> build/bdist.linux-armv7l/egg/mfrc522
copying build/lib/mfrc522/__init__.py -> build/bdist.linux-armv7l/egg/mfrc522
copying build/lib/mfrc522/SimpleMFRC522.py -> build/bdist.linux-armv7l/egg/mfrc522
byte-compiling build/bdist.linux-armv7l/egg/mfrc522/MFRC522.py to MFRC522.cpython-35.pyc
byte-compiling build/bdist.linux-armv7l/egg/mfrc522/__init__.py to __init__.cpython-35.pyc
byte-compiling build/bdist.linux-armv7l/egg/mfrc522/SimpleMFRC522.py to SimpleMFRC522.cpython-35.pyc
creating build/bdist.linux-armv7l/egg/EGG-INFO
copying mfrc522.egg-info/PKG-INFO -> build/bdist.linux-armv7l/egg/EGG-INFO
copying mfrc522.egg-info/SOURCES.txt -> build/bdist.linux-armv7l/egg/EGG-INFO
copying mfrc522.egg-info/dependency_links.txt -> build/bdist.linux-armv7l/egg/EGG-INFO
copying mfrc522.egg-info/requires.txt -> build/bdist.linux-armv7l/egg/EGG-INFO
copying mfrc522.egg-info/top_level.txt -> build/bdist.linux-armv7l/egg/EGG-INFO
zip_safe flag not set; analyzing archive contents...
creating 'dist/mfrc522-0.0.7-py3.5.egg' and adding 'build/bdist.linux-armv7l/egg' to it
removing 'build/bdist.linux-armv7l/egg' (and everything under it)
Processing mfrc522-0.0.7-py3.5.egg
Removing /usr/local/lib/python3.5/dist-packages/mfrc522-0.0.7-py3.5.egg
Copying mfrc522-0.0.7-py3.5.egg to /usr/local/lib/python3.5/dist-packages
mfrc522 0.0.7 is already the active version in easy-install.pth

Installed /usr/local/lib/python3.5/dist-packages/mfrc522-0.0.7-py3.5.egg
Processing dependencies for mfrc522==0.0.7
Searching for spidev==3.4
Best match: spidev 3.4
Processing spidev-3.4-py3.5-linux-armv7l.egg
spidev 3.4 is already the active version in easy-install.pth

Using /usr/local/lib/python3.5/dist-packages/spidev-3.4-py3.5-linux-armv7l.egg
Finished processing dependencies for mfrc522==0.0.7`

**Sample of trying to write**
`debian@scuttle:~/basics$ sudo python3 L1_rfid.py
Place RFID on RFID writer.
^CTraceback (most recent call last):
  File "L1_rfid.py", line 33, in <module>
    write_rfid("Hello World!")  # Write "Hello World!" to RFID
  File "L1_rfid.py", line 16, in write_rfid
    reader.write(text)          # Write data to RFID
  File "/usr/local/lib/python3.5/dist-packages/mfrc522-0.0.7-py3.5.egg/mfrc522/SimpleMFRC522.py", line 92, in write
  File "/usr/local/lib/python3.5/dist-packages/mfrc522-0.0.7-py3.5.egg/mfrc522/SimpleMFRC522.py", line 96, in write_no_block
  File "/usr/local/lib/python3.5/dist-packages/mfrc522-0.0.7-py3.5.egg/mfrc522/MFRC522.py", line 260, in MFRC522_Request
  File "/usr/local/lib/python3.5/dist-packages/mfrc522-0.0.7-py3.5.egg/mfrc522/MFRC522.py", line 206, in MFRC522_ToCard
  File "/usr/local/lib/python3.5/dist-packages/mfrc522-0.0.7-py3.5.egg/mfrc522/MFRC522.py", line 160, in Write_MFRC522
KeyboardInterrupt`

**Sample of trying to read**
`debian@scuttle:~/basics$ sudo python3 L1_rfid.py
^CTraceback (most recent call last):
  File "L1_rfid.py", line 24, in <module>
    sn, data = read_rfid()  # Read card serial number and data and store to sn and data variables
  File "L1_rfid.py", line 12, in read_rfid
    id, text = reader.read()    # Read RFID Serial Number and Data
  File "/usr/local/lib/python3.5/dist-packages/mfrc522-0.0.7-py3.5.egg/mfrc522/SimpleMFRC522.py", line 42, in read
  File "/usr/local/lib/python3.5/dist-packages/mfrc522-0.0.7-py3.5.egg/mfrc522/SimpleMFRC522.py", line 65, in read_no_block
  File "/usr/local/lib/python3.5/dist-packages/mfrc522-0.0.7-py3.5.egg/mfrc522/MFRC522.py", line 260, in MFRC522_Request
  File "/usr/local/lib/python3.5/dist-packages/mfrc522-0.0.7-py3.5.egg/mfrc522/MFRC522.py", line 223, in MFRC522_ToCard
  File "/usr/local/lib/python3.5/dist-packages/mfrc522-0.0.7-py3.5.egg/mfrc522/MFRC522.py", line 175, in ClearBitMask
  File "/usr/local/lib/python3.5/dist-packages/mfrc522-0.0.7-py3.5.egg/mfrc522/MFRC522.py", line 163, in Read_MFRC522
KeyboardInterrupt`

TWR2020, 2019-11-13:
Ground pin on the Beaglebone was discovered to be bent during troubleshooting.

Closed 2019-11-13.

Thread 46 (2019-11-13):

Issue using L1_servo.py

TheWhiteCollarPlayers, 2019-11-13:
Hardware setup:
     Beagle Bone Blue connected via 12V barrel jack to wall outlet for power.
     Continuous servo connected in correct wiring configuration to servo1 position on BeagleBone Blue

Software Setup:
     uncommented while loop in L1_servo.py returns the following in the console:
`/usr/local/lib/python3.5/dist-packages/rcpy-0.5.0-py3.5-linux-armv7l.egg/rcpy/__init__.py:116: UserWarning: > Robotics cape initialized
  warnings.warn('> Robotics cape initialized')
/usr/local/lib/python3.5/dist-packages/rcpy-0.5.0-py3.5-linux-armv7l.egg/rcpy/__init__.py:127: UserWarning: > Installing signal handlers
  warnings.warn('> Installing signal handlers')
ERROR: in rc_pru_shared_mem_ptr could not open /dev/mem: Permission denied
Need to be root to access PRU shared memory
ERROR in rc_servo_init, failed to map shared memory pointer
Traceback (most recent call last):
  File "L1_servo.py", line 10, in <module>
    import rcpy.servo as servo
  File "/usr/local/lib/python3.5/dist-packages/rcpy-0.5.0-py3.5-linux-armv7l.egg/rcpy/servo.py", line 2, in <module>
    from rcpy._servo import *
SystemError: initialization of _servo failed without raising an exception
Initiating cleanup...
Done with cleanup`

Troubleshooting steps taken:
    Ran the following command which successfully actuated the servo: `sudo rc_test_servos -s 1.5`
Ran check_installed.sh and let it run to completion, no problems.
Issue persists, assistance required. Thank you.

TheWhiteCollarPlayers, 2019-11-13:
Solved, needed to run L1 as sudo, now wondering how if I can import into my L2 as sudo?

Closed 2019-11-13.

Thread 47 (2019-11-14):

all around Beagle Connection issue

jessaggie, 2019-11-14:
We turned off the wifi in connman with the command connmanctl disable wifi and can no longer see anything when hard wired in through MOBA XTerm and through SSHing in.

jessaggie, 2019-11-14:
We were able to reenable the wifi access point through the serial port when hard wired in. When doing a normal boot after we were able to get on the beagle.

jessaggie, 2019-11-14:
Plug beaglebone into the computer through the USB port. Open up Moba Xterm and start a new terminal selecting serial connection. Select usb/uart and set the baud rate to 15000. After this run the commands below.
`connmanctl`
`agent on`
`enable wifi` (this is the most important one)
`scan wifi`
`services ` (should display an SSID address)
`connect (insert SSID address from above)`

dmalawey, 2019-11-15:
I'm glad it was a quick fix in the end!

Closed 2019-11-14.

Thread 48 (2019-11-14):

self installer issue with Debian 9.9

destantraeger, 2019-11-14:
Our SD card is flashed with version 9.9 of the appropriate Debian distribution and slf installer is no longer compatible. When part1 is run, it will throw this error and then reboot.

debian@beaglebone:/var/lib/cloud9$ cd ~
debian@beaglebone:~$ sudo bash self_installer_part1.sh
[sudo] password for debian:
10+0 records in
10+0 records out
10485760 bytes (10 MB, 10 MiB) copied, 1.01095 s, 10.4 MB/s
Already up-to-date.
Media: [/dev/mmcblk0]
sfdisk: 2.26.x or greater
Disk /dev/mmcblk0: 14.7 GiB, 15728640000 bytes, 30720000 sectors
Units: sectors of 1 * 512 = 512 bytes
Sector size (logical/physical): 512 bytes / 512 bytes
I/O size (minimum/optimal): 512 bytes / 512 bytes
Disklabel type: dos
Disk identifier: 0x672a5d88

Old situation:

Device         Boot Start      End  Sectors  Size Id Type
/dev/mmcblk0p1 *     8192 30719999 30711808 14.7G 83 Linux

>>> Created a new DOS disklabel with disk identifier 0xade4c5d5.
/dev/mmcblk0p1: Created a new partition 1 of type 'Linux' and of size 14.7 GiB.
Partition #1 contains a ext4 signature.
/dev/mmcblk0p2: Done.

New situation:

Device         Boot Start      End  Sectors  Size Id Type
/dev/mmcblk0p1 *     8192 30719999 30711808 14.7G 83 Linux

The partition table has been altered.
Calling ioctl() to re-read partition table.
Re-reading the partition table failed.: Device or resource busy
The kernel still uses the old table. The new table will be used at the next reboot or after you run partprobe(8) or kpartx(8).
Syncing disks.
reboot

ansarid, 2019-11-14:
Please send the output of "blkid -h".

destantraeger, 2019-11-14:
debian@beaglebone:~$ blkid -h
blkid from util-linux 2.29.2  (libblkid 2.29.2, 22-Feb-2017)
Usage:
 blkid -L <label> | -U <uuid>

 blkid [-c <file>] [-ghlLv] [-o <format>] [-s <tag>]
       [-t <token>] [<dev> ...]

 blkid -p [-s <tag>] [-O <offset>] [-S <size>]
       [-o <format>] <dev> ...

 blkid -i [-s <tag>] [-o <format>] <dev> ...

Options:
 -c <file>   read from <file> instead of reading from the default
               cache file (-c /dev/null means no cache)
 -d          don't encode non-printing characters
 -h          print this usage message and exit
 -g          garbage collect the blkid cache
 -o <format> output format; can be one of:
               value, device, export or full; (default: full)
 -k          list all known filesystems/RAIDs and exit
 -s <tag>    show specified tag(s) (default show all tags)
 -t <token>  find device with a specific token (NAME=value pair)
 -l          look up only first device with token specified by -t
 -L <label>  convert LABEL to device name
 -U <uuid>   convert UUID to device name
 -V          print version and exit
 <dev>       specify device(s) to probe (default: all devices)

Low-level probing options:
 -p          low-level superblocks probing (bypass cache)
 -i          gather information about I/O limits
 -S <size>   overwrite device size
 -O <offset> probe at the given offset
 -u <list>   filter by "usage" (e.g. -u filesystem,raid)
 -n <list>   filter by filesystem type (e.g. -n vfat,ext3)

On Thu, Nov 14, 2019 at 9:35 AM Daniyal Ansari <notifications@github.com>
wrote:

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

--
Destan Traeger
Texas A&M University - College Station, TX
Undergraduate Student | MXET
Cell: (210) 376-0343
destantraeger@tamu.edu

ansarid, 2019-11-15:
@destantraeger Please send the output of "lsblk".

ansarid, 2019-11-27:
Closing due to lack of response.

Closed 2019-11-27.

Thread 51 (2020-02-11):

Flow credentials file is encrypted in NodeRed

dneece5, 2020-02-11:
When trying to deploy the accelerometer chart in NodeRed of Lab 2, it gives us the following bug:
```
---------------------------------------------------------------------
Your flow credentials file is encrypted using a system-generated key.

If the system-generated key is lost for any reason, your credentials
file will not be recoverable, you will have to delete it and re-enter
your credentials.

You should set your own key using the 'credentialSecret' option in
your settings file. Node-RED will then re-encrypt your credentials
file using your chosen key the next time you deploy a change.
---------------------------------------------------------------------
```
It also opens a new tab with the following message:
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
Everything is setup correctly and everything is properly installed on the BeagleBoard, but we can't figure out why we can't create our accelerometer chart in NodeRed.

Closed 2020-02-15.

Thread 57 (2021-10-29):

Unable to track objects based off of RGB values on camera

connortolbert, 2021-10-29:
Howdy, I am using a Pi 3B and running the L2_track_target.py script and cannot get it to properly track RGB color combinations. I am using the image dated 2021-05-07 and have tested a multitude of different RGB combinations. I even tried testing them in different orders because I thought maybe they needed to be inputted in a different manner. I would like to be able to utilize this script to find and track objects based on RGB values and utilize the distance from the center printed out to follow a colored line made from tape
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
.

dmalawey, 2021-10-29:
Please tell us what hardware you're using, including the camera.

Please tell us the behavior you DO GET since you DON'T GET "properly tracking RGB"

Then, please tell your setup steps in enough detail so someone could repeat the issue.  @ansarid do you still have the link that explains how to clearly state a problem?

connortolbert, 2021-10-29:
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
I downloaded the L2_track_target.py script, added the variables shown above, and changed the pixel setup to 1920 x 1080 in L1_camera. Afterwards, I changed the get ratio function to divide by 1920 to get the correct values. Besides that all I did was change the variable being inserted to the function to test different colors in the L2_track_target.py script.

dmalawey, 2021-10-29:
Thanks @connortolbert now we are getting somewhere.  I think it's best to validate that your camera is producing the stream of jpeg images, before it gets pulled into python.  We have not tested the combo of Pi + Logitech C922 before.

Take a look at [this guide](https://scuttlerobot.org/uploads/SCUTTLE_Operation_Guide.pdf) in section 2.1, Module 1.  This manual is copyrighted and we are still adjusting it so don't distribute.

connortolbert, 2021-10-29:
Okay, thanks for the help!

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
--
Thank you,
Connor Tolbert

Closed 2021-11-09.

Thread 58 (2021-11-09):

Getting RCPY and PYCNTRL to Install Appropriately...

silver2row, 2021-11-09:
Hello,

Seth here. W/ GCC-10 on Bullseye, rcpy and pycntrl do not get installed appropriately. So, I am currently working on this issue.

...

If anyone has any recommendations, please reply.

Seth

dmalawey, 2021-11-15:
Hi @silver2row are you part of the beaglebone organization? We've had issues with rcpy for a long time and we were able to get some parts to work, while others were never resolved.  Are you here to help us? 😄

silver2row, 2021-11-15:
Hello...no. Sadly no. I am not affiliated w/ their organization.

Oh and by helping, you mean to alter source to work correctly w/ current changes in images, OSs, C standards, and C++ standards, maybe?

I might be able to help a bit.

@dmalawey , I may be able to make time to pitch in. I got their source to compile finally along w/ warnings in the Bullseye OS w/ kernel 5.10.x.

Also, I have a listed error/warning pastebin paste on this link in librobotcontrol: https://github.com/beagleboard/librobotcontrol/issues/213 .

Seth

P.S. I take my time and move slowly, i.e. so, I may be working at this for some time. If you guys have a direction on what needs to transpire first, please let me know. I will pitch in when I can.

dmalawey, 2021-11-18:
@silver2row some of your references have gone over my head, but we need a person versed in embedded linux plus standards in C++ etc as you mentioned, for sure!

The most recent critical issue was related to the rcpy motor driving function just quitting on us, and a couple of my team members were teaching the Mobile Robotics lab when this happened multiple times so they have more details than I. If we can reproduce this issue I'll share it with you.

In 2020 and 2021 we focused on getting the Raspberry Pi fully integrated on SCUTTLE but next year I heard Beagle will release a new Blue which uses the new Texas Instruments TDA4VM.   At this time I hope to test out many new features they offer.

silver2row, 2021-11-19:
@dmalawey ,

Okay...no issue. Well, if you guys are going to use the new BBBlue when it arrives, nice. I am waiting on it too!

Seth

P.S. Anyway, if something happens and I get things configured correctly, I will reply.

silver2row, 2021-12-02:
@dmalawey ,

I have not figured anything out just yet. I think I am highly unskilled at getting someone else's lib. to work. I have resorted back to 4.19.x to make things work on my BBBlue for now.

Seth

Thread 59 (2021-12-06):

Support BLDC / Field Orientated Control?

samuk, 2021-12-06:
Hi, nice project!

 Just starting a robot project on a much smaller footprint, some commonality with your project. Looking to use smaller motors than you, but could potentially add support for larger motors to the driver board we're developing if it's of interest.

More here: https://cloud.transition-space.org/s/KyTnsYjs4GRkXjZ

Not exactly an issue, but couldn't spot an email for you.

dmalawey, 2021-12-06:
Thanks for finding us!  You can email me at dmalawey at g mail dot com.  Taking a peek at your document this looks pretty elegant.  I'll be happy to read more about it.

Closed 2021-12-06.

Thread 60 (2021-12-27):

i2cdetect not enabling

dmalawey, 2021-12-27:
From testing on 12/26:

**Steps Taken**
~Fresh install of the raspberry pi image SCTL_PI_IMG_2021.07
~updates and upgrades
~delete SCUTTLE directory on the Pi
~git clone scuttlerobot/SCUTTLE
~try to run command "sudo i2cdetect -y -r l" and no result
~not sure what to try

```
SCUTTLE ~ ➜  sudo raspi-config
modprobe: ERROR: ../libkmod/libkmod.c:586 kmod_search_moddep() could not open moddep file '/lib/modules/5.10.17-v7l+/modules.dep.bin'
modprobe: FATAL: Module i2c-dev not found in directory /lib/modules/5.10.17-v7l+
SCUTTLE ~ ➜  sudo i2cdetect -y -r 1
sudo: i2cdetect: command not found
```

dmalawey, 2021-12-27:
I ran this and it looks like i2c detect works.  So, I think we need to add this install to the image.

`sudo apt-get install -y python-smbus`

ansarid, 2021-12-27:
@dmalawey

> ~Fresh install of the raspberry pi image SCTL_PI_IMG_2021.07

Please use the latest `11-06-2021_RPi_SCUTTLE_v0.21.1.img.xz` image. I'm about to create a new release(`12-27-2021_RPi_SCUTTLE_v0.21.2.img.xz`), so maybe wait for that one if you're going to reflash. I'm not sure what naming scheme `SCTL_PI_IMG_2021.07` is.

> ~delete SCUTTLE directory on the Pi
> ~git clone scuttlerobot/SCUTTLE

Are you just asking to remove the current SCUTTLE folder and clone it again from the latest source?

> ~try to run command "sudo i2cdetect -y -r l" and no result
> ~not sure what to try

I'll put a fix in the new image that installs `i2c-tools` which should resolve that issue. Not sure why that wasn't already included.

> I ran this and it looks like i2c detect works. So, I think we need to add this install to the image.
>
> `sudo apt-get install -y python-smbus`

That might have worked, but that's not the correct solution. This will be fixed in the latest image.

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

I was not able to reproduce this issue on the latest image.

dmalawey, 2021-12-28:
Do you have some log of what's installed in each image?  Can we produce this?

ansarid, 2021-12-28:
> Do you have some log of what's installed in each image? Can we produce this?

I have an installer script that installs all the required packages and tools.

Closed 2022-02-10.

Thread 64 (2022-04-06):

SICK LiDAR Data Inconsistent

lbbettinger, 2022-04-06:
Ranges of LiDAR Data points are coming in as 0 [distance angle]:
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
We were getting up to 10-15 0 values in a row earlier. This is while using a fully charged SCUTTLE battery pack. Using a bench-top power supply results in little to no errors.

Current (Temporary Wiring):
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
SICK LiDAR is connected to the motor controller's 12V terminals. These terminals are then connected to the battery pack. The Orange SICK LiDAR power cable is currently fairly long since wire routing is still undecided. I suspect the wiring is the issue.

dmalawey, 2022-04-06:
OK here are some things you can check:

1. check the voltage of the battery.  the PIC has voltage/power meters that plug into anderson connectors.  Make sure in your trials the voltage is matched between battery and power supply
3.  check your surroundings - run your 2 trials with matching surroundings. (dont move the bot)  If the lidar strikes a reflective surface it won't get a value back.  Same if the distance is above 10m (see datasheet)
4. Please define "fairly long cable" - also I don't recognize this orange cable as we purchased a set of high-quality cables for all of the LIDARS in MXET 300 which you can probably borrow.
5. Please define "little to no errors" - when you have errors what do they look like?
6. Please build a proper y-connector to split off your anderson power.  This configuration shown is not good practice.  We have videos for building splitters.

lbbettinger, 2022-05-02:
Shortening the cable and using Anderson Powerpole connectors resolved inconsistencies with the LiDAR

lbbettinger, 2022-05-02:
Shortening the cable and using Anderson Powerpole connectors resolved inconsistencies with the LiDAR

Closed 2022-05-02.

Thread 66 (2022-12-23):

Issue with Encoder

treshanappuhamy, 2022-12-23:
any idea why i get encoder readings failed. i checked all of the wirings
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

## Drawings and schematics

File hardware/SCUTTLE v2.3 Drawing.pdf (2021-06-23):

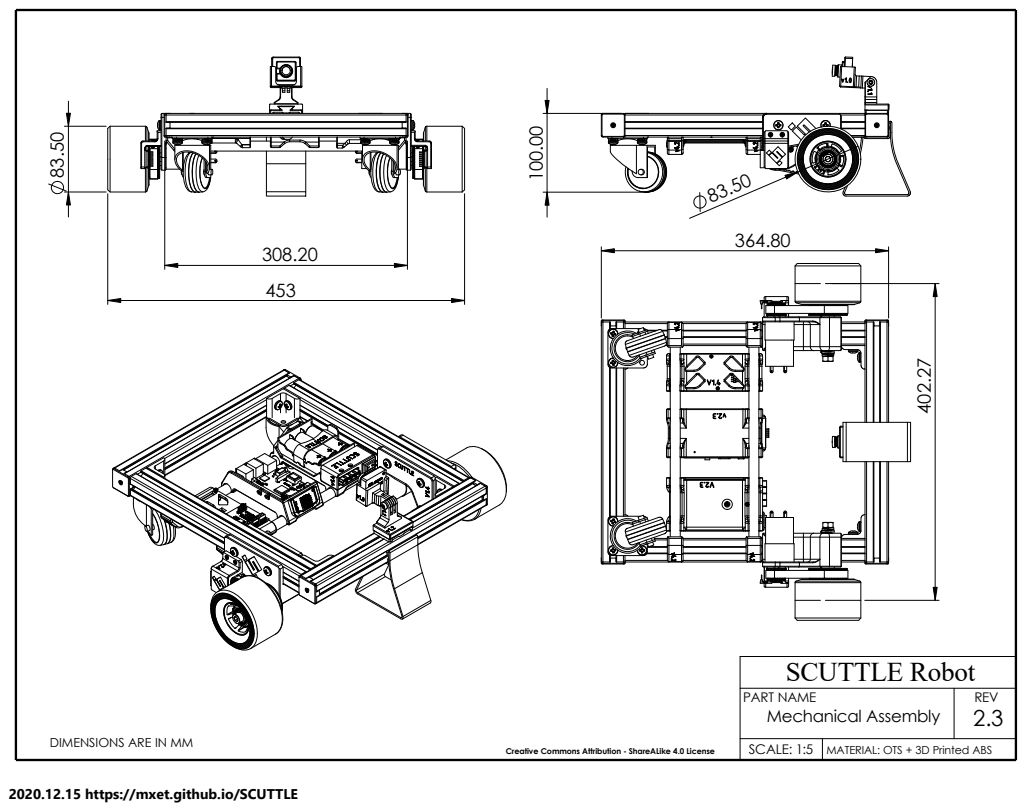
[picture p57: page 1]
SCUTTLE Robot; Creative Commons Attribution - ShareALike 4.0 License; MATERIAL: OTS + 3D Printed ABS

PART NAME Mechanical Assembly | REV 2.3

DIMENSIONS ARE IN MM
2020.12.15 https://mxet.github.io/SCUTTLE

SCALE: 1:5

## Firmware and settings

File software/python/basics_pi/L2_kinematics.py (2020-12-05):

# This program takes the encoder values from encoders, computes wheel movement
# and computes the movement of the wheelbase center based on SCUTTLE kinematics.
# This program runs on SCUTTLE with any CPU.

# THIS PROGRAM IS IN PROGRESS AS OF 2020.11 (DPM)

# Import external libraries
import numpy as np                          # library for math operations
import time                                 # library for time access

# Import local files
import L1_encoder as enc                    # local library for encoders

# define kinematics
R = 0.041                                   # wheel radius (meters)
L = 0.201                                   # half of wheelbase (meters)
res = (360/2**14)                           # resolution of the encoders (degrees per LSB)
pulleyRatio = 0.5                           # wheel movement per shaft movement
A = np.array([[R/2, R/2], [-R/(2*L), R/(2*L)]])     # This matrix relates [PDL, PDR] to [XD,TD]
wait = 0.02                                 # wait time between encoder measurements (s)


# Note:  this function takes at least 5.1ms plus "wait" to run.  It also populates a global
# variable so programs can access the previous measurement instantaneously.
def getPdCurrent():
    global pdCurrents                       # make a global var for easy retrieval
    encoders_t1 = enc.readShaftPositions()  # grabs the current encoder readings in degrees
    t1 = time.monotonic()                   # time.monotonic() reports in seconds
    time.sleep(wait)                        # delay for the specified amount
    
    encoders_t2 = enc.readShaftPositions()  # grabs the current encoder readings in degrees
    t2 = time.monotonic()                   # usually takes about .003 seconds gap
    global deltaT
    deltaT = round((t2 - t1), 3)            # compute delta-time (t.ttt scalar)

    # calculate travel of both wheels simultaneously
    travel = encoders_t2 - encoders_t1      # compute change in both shaft encoders (degrees)
    travel = encoders_t2 - encoders_t1      # array, 2x1 to indicate travel
    trav_b = travel + 360                   # array variant b
    trav_c = travel - 360                   # array variant c
    mx = np.stack((travel, trav_b, trav_c)) # combine array variants
    mx_abs = np.absolute(mx)                # convert to absolute val
    mins = np.argmin(mx_abs,0)              # find the indices of minimum values (left and right hand)
    left = mx[mins[0],0]                    # pull corresponding indices from original array
    right = mx[mins[1],1]                   # pull corresponding index for RH
    shaftTravel = np.array([left,right])    # combine left and right sides to describe travel (degrees)
    
    # build an array of wheel speeds in rad/s
    wheelTravel = shaftTravel * pulleyRatio     # compute wheel turns from motor turns
    wheelSpeeds_deg = wheelTravel / deltaT      # compute wheel speeds (degrees/s)
    pdCurrents = wheelSpeeds_deg * np.pi / 180  # compute wheel speeds (rad/s) & store to global variable
    return(pdCurrents)                          # returns [pdl, pdr] in radians/second


def getMotion():                            # this function returns the chassis speeds
    B = getPdCurrent()                      # store phidots to array B (here still in rad/s)
    C = np.matmul(A, B)                     # perform matrix multiplication
    C = np.round(C, decimals=3)             # round the matrix
    return(C)                               # returns a matrix containing [xDot, thetaDot]

def phiTravels(encoders_t1, encoders_t2):   # get travel of wheels [deg, deg] (take no measurements)
    travel = encoders_t2 - encoders_t1      # compute change in both shaft encoders (degrees)
    travel = encoders_t2 - encoders_t1      # array, 2x1 to indicate travel
    trav_b = travel + 360                   # array variant b
    trav_c = travel - 360                   # array variant c
    mx = np.stack((travel, trav_b, trav_c)) # combine array variants
    mx_abs = np.absolute(mx)                # convert to absolute val
    mins = np.argmin(mx_abs,0)              # find the indices of minimum values (left and right hand)
    left = mx[mins[0],0]                    # pull corresponding indices from original array
    right = mx[mins[1],1]                   # pull corresponding index for RH
    shaftTravel = np.array([left,right])    # combine left and right sides to describe travel (degrees)
    wheelTravel = shaftTravel * pulleyRatio # compute wheel turns from motor turns [deg,deg]
    return(wheelTravel)                     # return the movement

# THIS SECTION ONLY RUNS IF THE PROGRAM IS CALLED DIRECTLY
if __name__ == "__main__":
    while True:
        C = getMotion()  # This take approx 25.1 ms if the delay is 20ms
        print("xdot(m/s), thetadot (rad/s):", C, "\t","deltaT: ", deltaT)
        time.sleep(0.2)

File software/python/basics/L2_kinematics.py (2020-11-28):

# This program takes the encoder values from encoders, computes wheel movement
# and computes the movement of the wheelbase center based on SCUTTLE kinematics.
# This program runs on SCUTTLE with any CPU.

import L1_encoder as enc                    # local library for encoders
import numpy as np                          # library for math operations
import time                                 # library for time access

# define kinematics
R = 0.041                                   # wheel radius (meters)
L = 0.201                                   # half of wheelbase (meters)
res = (360/2**14)                           # resolution of the encoders (deg)
roll = int(360/res)                         # variable for rollover logic
gap = 0.5 * roll                            # degress specified as limit for rollover

A = np.array([[R/2, R/2], [-R/(2*L), R/(2*L)]])     # This matrix relates [PDL, PDR] to [XD,TD]

wait = 0.02                                 # wait time between encoder measurements (s)


def getTravel(deg0, deg1):                  # calculate the delta on Left wheel
    trav = deg1 - deg0                      # reset the travel reading
    if((-trav) >= gap):                     # if movement is large (has rollover)
        trav = (deg1 - deg0 + roll)         # forward rollover
    if(trav >= gap):
        trav = (deg1 - deg0 - roll)         # reverse rollover
    return(trav)


# Note:  this function takes at least 5ms to run.  It also populates a global
# variable so programs can access the previous measurement instantaneously.
def getPdCurrent():
    global pdCurrents                       # make a global var for easy retrieval
    encoders = enc.read()                   # grabs the current encoder readings in degrees
    degL0 = round(encoders[0], 1)           # reading in degrees.
    degR0 = round(encoders[1], 1)           # reading in degrees.
    t1 = time.time()                        # time.time() reports in seconds
    time.sleep(wait)                        # delay specified amount
    encoders = enc.read()                   # grabs the current encoder readings in degrees
    degL1 = round(encoders[0], 1)           # reading in degrees.
    degR1 = round(encoders[1], 1)           # reading in degrees.
    t2 = time.time()                        # reading about .003 seconds
    global deltaT
    deltaT = round((t2 - t1), 3)            # new scalar dt value

    # ---- movement calculations
    travL = getTravel(degL0, degL1) * res   # grabs travel of left wheel, degrees
    travL = -1 * travL                      # this wheel is inverted from the right side
    travR = getTravel(degR0, degR1) * res   # grabs travel of right wheel, degrees

    # build an array of wheel speeds in rad/s
    travs = np.array([travL, travR])        # stores the travel in degrees
    travs = travs * 0.5                     # pulley ratio = 0.5 wheel turns per pulley turn
    travs = travs * 3.14 / 180              # convert degrees to radians
    travs = np.round(travs, decimals=3)     # round the array
    wheelSpeeds = travs / deltaT
    wheelSpeeds = np.round(wheelSpeeds, decimals=3)
    pdCurrents = wheelSpeeds                # store the updated most recent wheel speeds to the class variable
    return(pdCurrents)                      # returns [pdl, pdr] in radians/second


def getMotion():                            # this function returns the chassis speeds
    B = getPdCurrent()                      # store phidots to array B (here still in rad/s)
    C = np.matmul(A, B)                     # perform matrix multiplication
    C = np.round(C, decimals=3)             # round the matrix
    return(C)                               # returns a matrix containing [xDot, thetaDot]

# THIS SECTION ONLY RUNS IF THE PROGRAM IS CALLED DIRECTLY
if __name__ == "__main__":
    while True:
        C = getMotion()
        print("xdot(m/s), thetadot (rad/s):", C)
        time.sleep(0.1)

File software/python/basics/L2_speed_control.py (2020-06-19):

# speed_control.py takes target speeds and generates duty cycles
# to send to motors, and has a function to execute PID control.

# Import external libraries
import numpy as np                                  # for handling arrays

# Import local files
import L1_motors as m                               # for controlling motors

# Initialize variables
u_integral = 0
DRS = 0.8                                           # direct rescaling - for open-loop motor duty
kp = 0.04                                           # proportional term
ki = 0.04                                           # integral term
kd = 0.0                                            # derivative term
pidGains = np.array([kp, ki, kd])                   # form an array to collect pid gains.

# a function for converting target rotational speeds to PWMs without feedback
def openLoop(pdl, pdr):
    DRS = 0.8                                       # create a variable for direct-re-scaling
    duties = np.array([pdl, pdr])                   # put the values into an array
    duties = duties * 1/9.75 * DRS                  # rescaling. 1=max PWM, 9.75 = max rad/s achievable
    duties[0] = sorted([-1, duties[0], 1])[1]       # place bounds on duty cycle
    duties[1] = sorted([-1, duties[1], 1])[1]       # place bounds on duty cycle
    return duties

def driveOpenLoop(pdTargets):                       # Pass Phi dot targets to this function
    duties = openLoop(pdTargets[0], pdTargets[1])   # produce duty cycles from the phi dots
    m.MotorL(duties[0])                             # send command to motors
    m.MotorR(duties[1])                             # send command to motors

def scalingFunction(x):                             # a fcn to compress the PWM region where motors don't turn
    if -0.222 < x and x < 0.222:
        y = (x * 3)
    elif x > 0.222:
        y = ((x * 0.778) + 0.222)
    else:
        y = ((x * 0.778) - 0.222)
    return y

def scaleMotorEffort(u):                            # send the control effort signals to the scaling function
    u_out = np.zeros(2)
    u_out[0] = scalingFunction(u[0])
    u_out[1] = scalingFunction(u[1])
    return(u_out)

def driveClosedLoop(pdt, pdc, de_dt):               # this function runs motors for closed loop PID control
    global u_integral
    e = (pdt - pdc)                                 # compute error

    kp = pidGains[0]                                # gains are input as constants, above
    ki = pidGains[1]
    kd = pidGains[2]

    # GENERATE COMPONENTS OF THE CONTROL EFFORT, u
    u_proportional = (e * kp)                                       # proportional term
    try:
        u_integral += (e * ki)                                      # integral term
    except:
        u_integral = (e * ki)                                       # for first iteration, u_integral does not exist

    u_derivative = (de_dt * kd)                                     # derivative term takes de_dt as an argument

    # CONDITION THE SIGNAL BEFORE SENDING TO MOTORS
    u = np.round((u_proportional + u_integral + u_derivative), 2)   # must round to ensure driver handling
    u = scaleMotorEffort(u)                                         # perform scaling - described above
    u[0] = sorted([-1, u[0], 1])[1]                                 # place bounds on the motor commands
    u[1] = sorted([-1, u[1], 1])[1]                                 # within [-1, 1]

    # SEND SIGNAL TO MOTORS
    m.MotorL(round(u[0], 2))                                        # must round to ensure driver handling!
    m.MotorR(round(u[1], 2))                                        # must round to ensure driver handling!
    return

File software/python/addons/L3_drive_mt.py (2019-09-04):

# Level 3 program for driving SCUTTLE and handling other tasks in parallel

# IMPORT EXTERNAL ITEMS
import time
import numpy as np # for handling matrices
import threading # only used for threading functions
import math

# IMPORT INTERNAL ITEMS
import L2_speed_control as sc # closed loop control. Import speed_control for open-loop
import L2_inverse_kinematics as inv #calculates wheel parameters from chassis
import L2_kinematics as kin    # calculates chassis parameters from wheels
import L2_log as log # log live data to local files
# import L2_obstacle as obs  # for detecting obstacles
# import L2_color_target as ct # for driving with computer vision tracking
import L1_text2speech as t2s # for speaking over aux port
import L1_gamepad as gp # for accessing gamepad directly
import L1_encoder as enc # for accessing encoders directly
import L1_bmp as bmp # for accessing bmp sensor onboard
import L1_adc as adc # for accessing adc sensor onboard
import L1_rssi as rssi # for accessing rssi value


# CREATE A THREAD FOR SPEAKING
def loop_speak( ID ):
    myStringA = "I am scuttle robot"
    myStringX = "the future of meka tronics"
    myStringY = "gig em aggies"
    while(1):
        signals = gp.getGP()
        if signals[6]==1: # A button is pressed
            t2s.say(myStringA)
        elif signals[7]==1: # X button is pressed
            t2s.say(myStringX)
        elif signals[5]==1: # B button is pressed
            temp = round(bmp.getTemp(),1)
            myStringB = "My brain temperature is" +str(temp)+ " degrees celsius."
            t2s.say(myStringB)
        elif signals[4]==1: # Y button is pressed
            t2s.say(myStringY)
        elif signals[11]==1: # rt button is pressed (button 7)
            adcData = adc.getADC()
            voltage = round(adcData[5],1)
            myString = "My battery strength is" +str(voltage)+ " volts."
            t2s.say(myString)
        elif signals[10]==1: 
            #myRSSI = rssi.get_rssi('wlan0')
            myRSSI = -71.4
            myString = "wifi rssi is" +str(myRSSI)+ " decibels."
            t2s.say(myString)
        time.sleep(0.020)
        
# CREATE A THREAD FOR DRIVING
def loop_drive( ID ):
    
    # initialize variables for control system
    t0 = 0
    t1 = 1
    e00 = 0
    e0 = 0
    e1 = 0
    dt = 0
    de_dt = np.zeros(2) # initialize the de_dt
    count = 0
    # initialize variables for color tracking
    color_range = np.array([[0, 180, 130], [10, 255, 255]])
    thetaOffset = 0
    # initialize driving mode
    mode = 0
    
    while(1):
        count += 1
        # THIS BLOCK IS FOR DRIVING BY COLOR TRACKING
        # colorTarget = ct.colorTarget(color_range) # use color tracking to generate targets
        # x = colorTarget[0]
        # if x != None:
        #     thetaOffset = ct.horizLoc(x) #grabs the angle of the target in degrees
        # myThetaDot = thetaOffset * 3.14/180 *2 # achieve centering in 0.5 seconds
        # print(myThetaDot)
        # myXDot = 0 # enable this line to freeze driving, and turn only.
        # myXDot = 
        # A = np.array([ myXDot, myThetaDot ])
        # pdTargets = inv.convert(A) # convert [xd, td] to [pdl, pdr]
        # print(pdTargets)
        
        # THIS BLOCK IS FOR CONSTANT SPEED DRIVING (NO CONTROL INPUT)
        # constantThetaDot = 1.5 # target, rad/s
        # constantXDot = 0.2 # target, m/sc
        # A = np.array([constantXDot, constantThetaDot])
        # myPhiDots = inv.convert(A)
       
        # THIS CODE IS FOR OPEN AND CLOSED LOOP control
        #pdTargets = np.array([9.7, 9.7]) #Fixed requested PhiDots; SPECIFICALLY FOR PID LAB
        pdTargets = inv.getPdTargets() # populates target phi dots from GamePad
        kin.getPdCurrent() # capture latest phi dots & update global var
        pdCurrents = kin.pdCurrents # assign the global variable value to a local var
       
        # THIS BLOCK UPDATES VARS FOR CONTROL SYSTEM
        t0 = t1  # assign t0
        t1 = time.time() # generate current time
        dt = t1 - t0 # calculate dt
        e00 = e0 # assign previous previous error
        e0 = e1  # assign previous error
        e1 = pdCurrents - pdTargets # calculate the latest error
        de_dt = (e1 - e0) / dt # calculate derivative of error
        
        # CALLS THE CONTROL SYSTEM TO ACTION
        signals = gp.getGP() # grab gamepad input
        if signals[14]: # check if mode button was pressed (Left stick)
            mode = not mode 
            time.sleep(1)
            #t2s.say("changing modes.")
        if mode == 0:
            sc.driveOpenLoop(pdTargets)
        else:
            sc.driveClosedLoop(pdTargets, pdCurrents, de_dt)  # call the control system
        time.sleep(0.05)
        
        
        u = sc.u 
        u_proportional = sc.u_proportional
        u_integral = sc.u_integral
        u_derivative = sc.u_derivative
        
        # THIS BLOCK OUTPUTS DATA TO A CSV FILE
        if count == 1:
            log.clear_file()
            log.csv_write([count,pdCurrents[0], pdTargets[0],u[0],u_integral[0],u_derivative[0]])
            #log.csv_write([count,pdCurrents[0], pdTargets[0], u[0]] )
        elif count > 1 and count <= 400:
            #log.csv_write([count,pdCurrents[0], pdTargets[0], u[0]])
            log.csv_write([count,pdCurrents[0],pdTargets[0],u[0],u_integral[0],u_derivative[0]])
            #print(count,pdCurrents[0], pdTargets[0])
        else:
            break

# CREATE A THREAD FOR SCANNING FOR OBSTACLES
def loop_scan( ID ):
    while(1):
        #d = obs.nearest_point() #returns the distance and the y-value of nearest obstacle
        #print("nearest point:", d)
        # if d[0] < 0.15: #if the nearest obstacle less than 10cm
        #         t2s.say("NO")
        time.sleep(0.1)

# ALL THREADS ARE CALLED TO RUN IN THE MAIN FUNCTION
def main():

        print("starting the main fcn")
        threads = []  # create an object for threads

        t = threading.Thread( target=loop_speak, args=(1,) ) # make 1st thread object
        threads.append(t)
        t.start()
        print("started thread1")

        t2 = threading.Thread( target=loop_drive, args=(2,) ) # make 2nd thread object
        threads.append(t2)
        t2.start()
        print("started thread2")

        t3 = threading.Thread( target=loop_scan, args=(3,) ) # make 2nd thread object
        threads.append(t3)
        t3.start()
        print("started thread3")

        # the join commands manipulate the way the program concludes multithreading.
        t.join()
        t2.join()
        t3.join()

main()

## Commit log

2019-02-11 Pulley revised for thick-spoke wheels
    [wheelPulley_V2_mod1.STL]
2019-02-11 wheel pulley for thick-spoke wheels
    [wheelPulley_V2_mod1.sldprt]
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2019-02-15 Updated tubes, 3030 tabs, & motor driver ASIN
    Part No's updated for 12.7mm tube (previous tube was too small diameter). 3030 tab/nut part number changed, motor driver ASIN was corrected.
2019-02-19 The shaft holes custom size
    The shaft holes for these plates are 7.8mm to achieve 8mm size after laser cut from 1/4" acrylic sheet.
    [plate1 acrylic v1.0.DXF, plate2 acrylic v1.0.DXF]
2019-02-28 updating motor driver bracket
    [MotorDriverBracket V1.1.STL]
2019-02-28 update motor driver bracket
    [DualMotorDriverMount.SLDPRT]
2019-02-28 update bb bracket - v2.1
    [bbbBracket V2.1.STL]
2019-02-28 update rail bracket -v2.1
    [RailBracket V2.1.STL]
2019-03-08 Moved turn and motor speed functions from scuttle.py and scuttle_HL.py to here.
2019-03-08 Removed turning and motor speed functions
    Both functions have been moved to drive.py.
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2019-04-01 Modified layout
    [18650 battery.SLDPRT, 30mm rail.sldprt, 3cellPack.SLDASM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]
2019-04-08 move files
    [BatteryBracket V1.1.STL, BatteryBracketLid V1.1.STL, BatteryBracketLid V1.STL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]
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2019-04-10 Moved BOM to hardware instead of CAD since it is not a CAD file and pertains to all hardware.
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2019-05-16 first revision of pi mounting bracket
    [PiMount V1.0.STL]
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2019-05-17 currently broken - in progress to make function
    [gamepad_ex1.py]
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2019-05-24 fixed gamepad code, simplified
    [joystick_drive.py]
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2019-06-27 Add files via upload
    This part is intended to be printed with no infill, four perimeter layers and zero top and bottom solid layers. 0.25mm layer thickness is good. The resulting part will print quickly, with flexibility to snap onto the 30x30mm rail.
    [wheelStand v1.2.STL]
2019-06-27 Add files via upload
    Print with 4 perimeter layers, 0 top and bottom solid layers, and 0% infill to achieve fast print and compliant snap-fit
    [wheelStand v1.2.STL]
2019-06-27 Add files via upload
    This component snaps into the 3030 rail. It's designed to be glued to decorative plates, logos, etc.
    [snapIn v2.1.STL]
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2019-07-18 common encoder mounting holes for L & R
    [EncoderBracket V2.3.STL]
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2019-09-04 updated color tracking code. Fixed text placement in mjpg streamer filter.
    [L2_color_target.py]
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2019-09-04 Fixed passing None Type to horizLoc
    [L2_color_target.py, L2_track_target.py]
2019-09-10 replace both wheel plates & spacer with a 3D print
    [uni_bracket_R 43.72.100mm v1.3.STL]
2019-09-10 replace both wheelplates & spacer with a 3d print
    [uni_bracket_L 43.72.100mm v1.3.STL]
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2019-09-11 Flexible Wing Universal Bracket
    [universal bracket V3.2.STL]
2019-09-11 updated battery bracket
    [BatteryBracket v1.2_127.65.32mm.STL]
2019-09-11 update battery bracket
    [BatteryBracket v1.3_127.65.32mm.STL]
2019-09-12 update battery lid
    [BatteryLid v1.2_119.65.32mm.STL]
2019-09-12 update bbb bracket
    [bbbBracket V2.2_122.31.62mm.STL]
2019-09-12 update camera bracket
    [CameraBracket v2.1_53.54.29mm.STL]
2019-09-12 update encoder bracket
    [EncoderBracket v2.4_26.48.31mm.STL]
2019-09-17 updated rod bracket
    [rodBracket v4.0_40.27.20mm.STL]
2019-09-17 new motor pulley - flange removed
    [MotorPulleyV2.2_15.26.26mm.STL]
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2019-09-24 add the snap-in clip for 30x30 rails
    [snap-in v1.3.STL]
2019-09-24 fix outdated function call (getPhiDots)
    [L2_kinematics.py]
2019-09-25 correct (2*L) in A-matrix
    [L2_kinematics.py]
2019-09-25 correction on slide indicating encoder pcb config
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2019-09-30 One STL with 2 UniBrackets & 2 Encoder Brackets
    [UniBracketPair.STL]
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2019-10-08 switched to correct rc522 wiring diagram
2019-10-14 one STL with four rod brackets
    [RodBracketSet v4.STL]
2019-10-14 1 STL with battery, bbb, and mtr drvr brackets
    [bracketPacket.STL]
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2019-10-30 upload jointHoop
    [JointHoop v1.STL]
2019-10-30 add clasp
    [Clasp v1.2.STL]
2019-10-30 add servoSeat
    [ServoSeat v1.STL]
2019-10-30 add towerMount
    [TowerMount v1.STL]
2019-10-30 add puckBracket
    [PuckBrkt v2.STL]
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2019-11-21 correction to ultrasonic sensor wiring
2019-12-11 new camera bracket - compact, more clearance
    [CameraBracket v2.3.STL]
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2020-07-27 omit B11 button due to error on rPi
    [L1_gamepad.py]
2020-07-30 removed solidworks designs folder
    [18650 battery.SLDPRT, 30mm rail.sldprt, 3cellPack.SLDASM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]
2020-07-30 removed laser cutting folder
    [plate1 acrylic v1.0.DXF, plate2 acrylic v1.0.DXF]
2020-07-30 removed solidworks designs alternate
    [wheelPulley_V2_mod1.sldprt]
2020-07-30 removed servo arm folder
    [Clasp v1.2.STL, JointHoop v1.STL, PuckBrkt v2.STL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]
2020-07-30 removed forklift folder
    [Pulley_GT2_20t.SLDPRT, bracket_90deg_20mm.SLDPRT, crate.V1.SLDPRT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]
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2020-09-13 latest i2c bracket
    [i2cBracket v2.3.STL]
2020-09-13 upload correct i2c bracket
    [i2cBracket v2.0.STL]
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2020-09-23 reoriented label
    [WheelBracket_L v1.3.STL]
2020-09-23 updated motor pulley
    [motorPulleyV2.5.STL]
2020-09-27 battery brkt - improve fit, reorient version no.
    [batteryBracket v1.4.STL]
2020-09-28 added kickStand STL
    [kickStand v1.4.STL]
2020-10-08 added L298N, fix errors (wiring guide)
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2020-11-01 add new version of battery pack STL files (3)
    [batteryHoop v2.3.STL, batteryMount v2.3.STL, batteryPanel v1.3.STL]
2020-11-03 upload alternate rod bracket 4.1b
    this component is for the malaysian variant of aluminum extrusions
    [rodBracket v4.1b.STL]
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2020-11-03 add cornerBracket STL file
    [cornerBracket v1.0.STL]
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2020-12-02 upload printable end cap STL file
    [endCap v2.2.STL]
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2021-06-03 rewriten L1_gamepad.py to no longer use pygame
    [L1_gamepad.py]
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2021-09-28 better missing gamepad handling
    [L1_gamepad.py]
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2021-10-21 new camera bracket for square cam
    [cameraBracket v3.STL]
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2021-10-27 updated battery mount bottom holes
    [batteryMount v2.4.STL]
2021-10-27 camera bracket chamfer & upgrade to 3MF format
    [cameraBracket v3.0.3MF]
2021-10-27 dovetail - increae finger gap 3.1 to 3.3mm
    [doveTailC_v1.3.3MF]
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2021-12-13 wiring corrections, graphics upgrade
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2021-12-23 assy guide: corrections to pulleys spec
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2021-12-26 pi wiring corrections
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2021-12-27 updated STL files to 3MF
    [btryBrkt_v2.4.3MF, btryHoop_v2.3.3MF, btryPanel_v1.4.3MF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]
2021-12-28 Upload 3D Prints into new folder
    [btryBrkt_v2.4.3MF, btryHoop_v2.3.3MF, btryPanel_v1.4.3MF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]
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2022-06-16 sctl wrench update
    increased hex from 13.3 to 13.55mm
    [sctlWrch_v1.4.STL]
2022-10-07 encrBrkt v2.8 increases gap +1mm
    [encdrBrkt_v2.8.STL]
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2022-11-16 Delete encdrBrkt_v2.7.STL
    Deleting Encoder Bracket v2.7. To Access this file, v2.7, see repo history. v2.7 is 1mm closer to the motor Pulley in design.
    [encdrBrkt_v2.7.STL]
2022-11-16 update wrench STL filename
    [wrench_v2.0.STL]
2023-02-09 motor pulley updated
    adjust inner hole shape; match tolerance on diameter and flat.
    [mtrPuly_v3.4.STL]
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
